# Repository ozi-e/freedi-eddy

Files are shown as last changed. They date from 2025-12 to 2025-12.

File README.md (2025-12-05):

# freedi-eddy
Adding an eddy duo probe to the qidi x-max 3 running latest freedi

I will probably add additional configurations later as I'm working on adding the LH Pico MMU also

## How to use:
### 1 - Print the bracket
I used ASA filament, it prints well without supports, I suggest adding a brim and also printing the first layer at 15mm/s
Bracket requires 2x M3 inserts

### 2 - Take off the toolhead front and back covers
Self explanatory

### 3 - Route the cable
Note: I had an idea to use an Adafruit USB C hub to chain the probe together with the toolhead, but it took a while to arrive so I used the Eddy USB cable
Route the USB cable through the e-chain, start from the toolhead and route it to the mainboard.
Roll the overlength of the cable into an "8" (don't coil it up).

### 4 - Remove the BLTouch/Inductive probe.
Screws will be re-used. You can disconnect the probe.

### 5 - Mount the Eddy probe
#### 5.1 - Remove the Eddy probe covers
#### 5.2 - Put the back cover back on, then screw it into the bracket
#### 5.3 - Mount the bracket onto the toolhead

### 6 - Back up your original config, then add or merge mine. Make sure to copy both the printer.cfg and the macros.cfg

### 7 - Add the device paths to the config
#### 7.1 - Copy the MCU toolhead path from your backup into the [mcu Toolhead] section of the new printer.cfg, then save (no restart)
#### 7.2 - In Mainsail, go to "Machine" -> "Devices" -> "Serial" -> "Refresh"
#### 7.3 - Copy the rp2040 "Path by ID" (probably on ttyACM1 if you have nothing else connected) and paste it into [mcu eddy] section of printer.cfg
#### 7.4 - Save and restart

### 8 - Copy over the begin and end codes
#### 8.1 - Paste the contents of begin_code.txt into your slicer begin code
#### 8.2 - Paste the contents of end_code.txt into your slicer end code

### 9 - Calibrate by following steps 2 through 4 (or 5 as required) from the Eddy probe onwards: https://github.com/bigtreetech/Eddy?tab=readme-ov-file#2-drive-current-calibration
Note: I already included some values regarding calibration, you should still redo everything as no 2 machines are the same
Note2: I increment the drive "reg_drive_current" to 16, your mileage may vary, check the FAQ section of the Eddy github link

### 10 - Do a test print, let me know what glitches you encounter

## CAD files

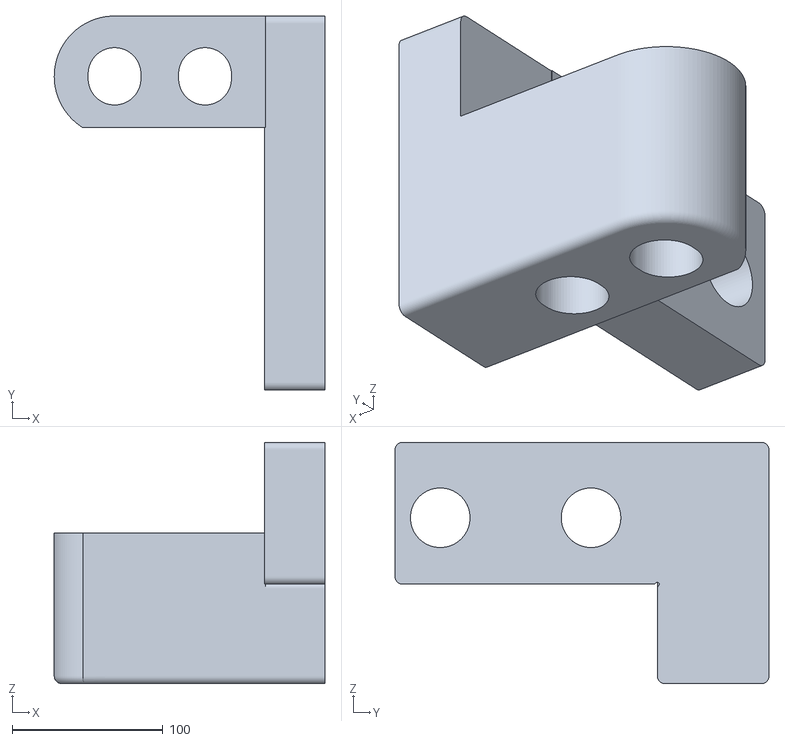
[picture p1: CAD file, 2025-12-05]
bracket.stl
179.4 x 248.0 x 160.0

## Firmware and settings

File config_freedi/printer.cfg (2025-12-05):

# X-Max3 config created by Phil1988(github)/coco.33(discord) on 20.12.2024
# For more information check out my wiki: https://github.com/Phil1988/FreeDi/wiki


#####################################################################
# Kinematics
#####################################################################
[printer]
kinematics:corexy
max_velocity: 600
max_accel: 20000
max_z_velocity: 20
max_z_accel: 500
square_corner_velocity: 8


#####################################################################
# Motherboard and periphery
#####################################################################
[temperature_sensor Mainboard_RK3328]
sensor_type: temperature_host
min_temp: 10
max_temp: 100

[mcu]
serial: /dev/ttyS0
restart_method: command
#baud: 500000

[temperature_sensor Mainboard_STM32F402]
sensor_type: temperature_mcu
sensor_mcu: mcu

[mcu Toolhead]
serial: /dev/serial/by-id/usb-Klipper_rp2040_E5D44D15290F5158-if00

[temperature_sensor Toolhead_RP2040]
sensor_type: temperature_mcu
sensor_mcu: Toolhead
min_temp: 0
max_temp: 100


#####################################################################
# Features
#####################################################################
# For saving GCODE files
[virtual_sdcard]
path: ~/printer_data/gcodes
on_error_gcode: CANCEL_PRINT

# For enabling pause/resume
[pause_resume]

# Activating exclude objects feature
[display_status]
[exclude_object]

# Expanding idle timeout
[idle_timeout]
timeout: 5400   ; 90min timeout

# Activating GCODE arc feature
[gcode_arcs]
resolution: 1.0

# Allowing free move (can be dangerous!)
[force_move]
enable_force_move: True

# Activating responses
[respond]
default_type: echo


#####################################################################
# FreeDi
#####################################################################
[include freedi.cfg] 


#####################################################################
# Macros
#####################################################################
[include macros.cfg]
#[include sp_mmu.cfg]


#####################################################################
# Input shaping
#####################################################################
[resonance_tester]
accel_chip:adxl345
probe_points:
    160, 160, 10
accel_per_hz: 75
sweeping_period: 0
max_smoothing: 0.5
    
[adxl345]
cs_pin: Toolhead:gpio13
spi_software_sclk_pin: Toolhead:gpio14
spi_software_mosi_pin: Toolhead:gpio15
spi_software_miso_pin: Toolhead:gpio12
axes_map: -x, z, -y

[input_shaper]
#shaper_type_x: mzv
#shaper_freq_x: 57.6
#shaper_type_y: mzv
#shaper_freq_y: 46.6


#####################################################################
# Hotend
#####################################################################
[extruder]
step_pin: Toolhead:gpio5
dir_pin: Toolhead:gpio4
enable_pin: !Toolhead:gpio10
rotation_distance: 53.5
gear_ratio: 1628:170
microsteps: 16
full_steps_per_rotation: 200
nozzle_diameter: 0.400
filament_diameter: 1.75
min_temp: 0
max_temp: 360
min_extrude_temp: 0
smooth_time: 0.000001
step_pulse_duration:0.000002

heater_pin: Toolhead:gpio0
sensor_type:MAX6675
sensor_pin: Toolhead:gpio17
max_power: 1.0
#control: pid  
#pid_Kp: 24.737
#pid_Ki: 10.994
#pid_Kd: 13.915

spi_speed: 100000
spi_software_sclk_pin: Toolhead:gpio18
spi_software_mosi_pin: Toolhead:gpio19
spi_software_miso_pin: Toolhead:gpio16

pressure_advance: 0.032
pressure_advance_smooth_time: 0.03
max_extrude_cross_section:5
instantaneous_corner_velocity: 10.000
max_extrude_only_distance: 1000
max_extrude_only_velocity: 130
max_extrude_only_accel: 3000

[verify_heater extruder]
max_error: 120
check_gain_time: 20
hysteresis: 5
heating_gain: 1


#####################################################################
# Heated bed
#####################################################################
[heater_bed]
heater_pin: PC8
sensor_type: NTC 100K MGB18-104F39050L32
sensor_pin: PA0
max_power: 1.0
#control: pid
#pid_kp: 64.431
#pid_ki: 2.845
#pid_kd: 364.839
min_temp: -50
max_temp: 125
pwm_cycle_time: 0.02 # for 50Hz line power 
#pwm_cycle_time: 0.016 # for 60Hz line power

[verify_heater heater_bed]
max_error: 200
check_gain_time: 360
hysteresis: 5
heating_gain: 1


#####################################################################
# Bed mesh
#####################################################################
#[bed_mesh]
#speed: 150               
#horizontal_move_z: 2.6   
#mesh_min: 28,8        
#mesh_max: 315,310     
#probe_count: 9,9     
#algorithm: bicubic
#bicubic_tension: 0.2
#mesh_pps: 4, 4


#####################################################################
# Probe
#####################################################################
#!# Pay attention to this section and compare it with your stock backup config
#[probe]
#pin: ^!Toolhead:gpio11
#x_offset: 28
#y_offset: 4.4
##z_offset: 1.890
#speed: 5
#samples: 2
#samples_result: average
#sample_retract_dist: 1.5
#samples_tolerance: 0.08
#samples_tolerance_retries: 3


#####################################################################
# Heated chamber
#####################################################################
[heater_generic chamber]
heater_pin: PB10
max_power:1.0
sensor_type:NTC 100K MGB18-104F39050L32
sensor_pin: PA1
control: watermark
max_delta: 1.0
min_temp:-100
max_temp:70

[verify_heater chamber]
max_error: 300
check_gain_time:480
hysteresis: 5
heating_gain: 1


########################################
# Filament runout sensor
########################################
[filament_switch_sensor filament]
switch_pin: ^Toolhead:gpio21
pause_on_runout: True
runout_gcode:
            M118 Filament run out!
event_delay: 3.0
pause_delay: 0.5


#####################################################################
# Fans
#####################################################################
## Part cooling fan 
# [fan_generic partfan]
# pin: Toolhead:gpio2
# max_power: 1.0
# cycle_time: 0.0100
# hardware_pwm: false
# kick_start_time: 0.200
# off_below: 0.08
# shutdown_speed: 0
[fan]
pin: Toolhead:gpio2
max_power: 1.0
cycle_time: 0.0100
hardware_pwm: false
kick_start_time: 0.200
off_below: 0.08
shutdown_speed: 0.0

## Big side radial turbo fan
[fan_generic sidefan]
pin: PA8
max_power: 1.0
cycle_time: 0.0100
hardware_pwm: false
kick_start_time: 0.250
off_below: 0.3
shutdown_speed: 0

## Activated charcoal blowing fan
[fan_generic filterfan]
pin: PC9
max_power: 1.0
cycle_time: 0.0100
hardware_pwm: false
kick_start_time: 0.200
off_below: 0.3
shutdown_speed: 0

## Cold end and toolhead housing fans
[heater_fan hotend_fan]
pin: Toolhead:gpio1
max_power: 1.0
shutdown_speed:1.0
kick_start_time: 0.5
heater: extruder
heater_temp: 50.0
fan_speed: 1.0
off_below: 0

#!# Delete the next section if your stock backup config doesnt have it
# Toolhead cooling fan
[heater_fan hotend_fan2]
pin: Toolhead:gpio20
max_power: 1.0
kick_start_time: 0.5
heater: extruder
heater_temp: 50.0
fan_speed: 1.0
off_below: 0

#!# Delete the next section if your stock backup config doesnt have it
## Controllable Mainboard cooling fan
[temperature_fan Mainboard_fan]
sensor_type: temperature_host 
pin: PC4        
max_power: 1.0  
cycle_time: 0.01
sensor_type: temperature_combined
sensor_list: temperature_sensor Mainboard_RK3328, temperature_sensor Mainboard_STM32F402
combination_method: max                                           # use the maximum reading of the sensors
maximum_deviation: 999.9                                          # we don't care about the difference in temperature
shutdown_speed: 0.0
kick_start_time: 0.4
off_below: 0.19
min_temp: 0
max_temp: 85.0  
target_temp: 42.0
min_speed: 0
max_speed: 1.0
control: pid
pid_deriv_time: 2.0
pid_Kp: 2.0
pid_Ki: 5.0
pid_Kd: 0.5


#####################################################################
# Light
#####################################################################
## caselight LEDs
[output_pin caselight]
pin: PC7
pwm: true
cycle_time: 0.0100
shutdown_value:0
value:1


#####################################################################
# Buzzer
#####################################################################
## Buzzer
[output_pin buzzer]
pin: PA2
pwm: false
shutdown_value:0
value:0

[output_pin sound]
pin: PA13
value:0


#####################################################################
# Power outage shutdown
#####################################################################
[output_pin pwc]
pin: PA3
pwm: False
value: 1
shutdown_value: 1


#####################################################################
# Drives
#####################################################################
[stepper_x]
step_pin: PB4
dir_pin: PB3
enable_pin: !PB5
microsteps: 32
rotation_distance: 39.94
full_steps_per_rotation: 200 
endstop_pin: tmc2209_stepper_x:virtual_endstop
position_min: -4
position_endstop: 334
position_max: 334
homing_speed: 40
homing_retract_dist: 0
homing_positive_dir: True
step_pulse_duration: 0.000002
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

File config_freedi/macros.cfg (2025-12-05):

#####################################################################
# Advanced CHAMBER_TEMP_CONTROLLER
#####################################################################

[gcode_macro SET_PRINT_STATS_INFO]
rename_existing: BASE_SET_PRINT_STATS_INFO_BASE
gcode:
    #TIMELAPSE_TAKE_FRAME
    BASE_SET_PRINT_STATS_INFO_BASE {rawparams}
    CHAMBER_TEMP_CONTROLLER

# Safety macro that gets frequently called by SET_PRINT_STATS_INFO to prevent too high chamber temperatures
[gcode_macro CHAMBER_TEMP_CONTROLLER]
gcode:
    {% set chamber_target_temp = printer['heater_generic chamber'].target %}
    {% set chamber_temp = printer['heater_generic chamber'].temperature %}
    {% if chamber_temp > printer.configfile.settings['heater_generic chamber'].max_temp %}
        M106 P3 S255
    {% else %}
        {% if chamber_target_temp > 0 %}
            # Allow for 3C of "grace" before we start ramping the exhaust fan speed
            # This prevents the macro from fighting with the chamber heater PID algorithm
            {% set difference = chamber_temp - (chamber_target_temp + 3) %}
            {% if difference > 0 %}
                {% set filterfan_speed = ([(difference * 50), 255] | min) | int %}
                M106 P3 S{filterfan_speed}
            {% else %}
                M106 P3 S0
            {% endif %}
        {% endif %}
    {% endif %}
    
    
#####################################################################
# Homing modification
#####################################################################
[gcode_macro G28]
rename_existing: G28.1
gcode:
    {% set reduced_current_x = 0.6 %}
    {% set reduced_current_y = 0.7 %}
    {% set home_all = ('X' in rawparams.upper() and 'Y' in rawparams.upper() and 'Z' in rawparams.upper()) or 
                      ('X' not in rawparams.upper() and 'Y' not in rawparams.upper() and 'Z' not in rawparams.upper()) %}
    {% set home_current_x = printer.configfile.settings['tmc2209 stepper_x'].run_current * reduced_current_x %}
    {% set home_current_y = printer.configfile.settings['tmc2209 stepper_y'].run_current * reduced_current_y %}

    {% set init_XY_move = 30 %}
    #{% set y_init_move = 5 %}
    {% set z_clearance = 2 %}

    {% set home_all_final_position_x = printer.toolhead.axis_maximum.x / 2 %}
    {% set home_all_final_position_y = printer.toolhead.axis_maximum.y - 40 %}
    {% set home_all_final_position_z = 20 %}

    # If homing should at least move X or Y axis
    {% if home_all or 'X' in rawparams.upper() or 'Y' in rawparams.upper() %}     
        # Check if Z is homed
        {% if 'z' in printer.toolhead.homed_axes %}
            {% set Z_axis_was_homed = true %}                                                                       ; Set Z_axis_was_homed to true if Z is already homed
            G91                                                                                                     ; Use relative positioning
            G1 Z2 F600                                                                                              ; Move bed down
            G90                                                                                                     ; Use absolute positioning
        {% else %}
            {% set Z_axis_was_homed = false %}                                                                      ; Set Z_axis_was_homed to false if Z is not homed
            FORCE_MOVE STEPPER=stepper_z DISTANCE={z_clearance} VELOCITY=10                                         ; Move bed down
        {% endif %}
    {% endif %}

    {% if home_all or 'X' in rawparams.upper() or 'Y' in rawparams.upper() %} 
        G91                                                                                                         ; Use relative positioning
        FORCE_MOVE STEPPER=stepper_x DISTANCE={init_XY_move} VELOCITY=40                                            ; Move X a little before homing
        SET_KINEMATIC_POSITION X={printer.toolhead.position.x + (init_XY_move/2)}                                   ; Compensate the FORCE_MOVE position 
        SET_KINEMATIC_POSITION Y={printer.toolhead.position.y + (init_XY_move/2)}                                   ; Compensate the FORCE_MOVE position 
        G90                                                                                                         ; Use absolute positioning
    {% endif %}

    # Home X
    {% if home_all or 'X' in rawparams.upper() %}        
        SET_TMC_CURRENT STEPPER=stepper_x CURRENT={home_current_x}                                                  ; Lower motor current
        SET_TMC_CURRENT STEPPER=stepper_y CURRENT={home_current_x}                                                  ; Lower motor current
        G28.1 X                                                                                                     ; Home X
        SET_TMC_CURRENT STEPPER=stepper_x CURRENT={printer.configfile.settings['tmc2209 stepper_x'].run_current}    ; Set motor current to the previous value
        SET_TMC_CURRENT STEPPER=stepper_y CURRENT={printer.configfile.settings['tmc2209 stepper_y'].run_current}    ; Set motor current to the previous value
        #G1 X290 F1200                                                                                                ; Move X-axis slightly
        #G91
        #G1 X-10 F1200
        #FORCE_MOVE STEPPER=stepper_y DISTANCE=-10 VELOCITY=40
        #G90
    {% endif %}
    
    # Home Y
    {% if home_all or 'Y' in rawparams.upper() %}
        SET_TMC_CURRENT STEPPER=stepper_x CURRENT={home_current_y}                                                  ; Lower motor current
        SET_TMC_CURRENT STEPPER=stepper_y CURRENT={home_current_y}                                                  ; Lower motor current
        G28.1 Y                                                                                                     ; Home Y
        SET_TMC_CURRENT STEPPER=stepper_x CURRENT={printer.configfile.settings['tmc2209 stepper_x'].run_current}    ; Set motor current to the previous value
        SET_TMC_CURRENT STEPPER=stepper_y CURRENT={printer.configfile.settings['tmc2209 stepper_y'].run_current}    ; Set motor current to the previous value
        #G1 Y10 F1200                                                                                                ; Move Y-axis slightly
        #G91
        #G1 Y10 F1200
        #FORCE_MOVE STEPPER=stepper_y DISTANCE=-10 VELOCITY=40
        #G90
    {% endif %} 

    # Raise the bed again if only X or only Y axes were homed
    {% if not (home_all or 'Z' in rawparams.upper()) %}
        {% if Z_axis_was_homed %}
            G91                                                                                                     ; Use relative positioning
            G1 Z-2 F600                                                                                             ; Raise the bed back again
            G90                                                                                                     ; Use absolute positioning
        {% else %}
            FORCE_MOVE STEPPER=stepper_z DISTANCE=-{z_clearance} VELOCITY=10                                        ; Raise the bed back again
        {% endif %}
    {% endif %}

    # Home Z
    {% if home_all or 'Z' in rawparams.upper() %}
        G28.1 Z                                                                                                     ; Home Z
        G90                                                                                                         ; Set absolute positioning
        G1 Z{home_all_final_position_z}                                                                             ; Move bed down
    {% endif %}

    # Move to the final position if all axes were homed
    {% if home_all %}
        G90                                                                                                         ; Set absolute positioning
        G1 X{home_all_final_position_x} Y{home_all_final_position_y} Z{home_all_final_position_z} F7800             ; Move to the rear center
    {% endif %}


# Unconditional stop
[gcode_macro M0]
gcode:
    PAUSE


# Pause SD print
[gcode_macro M25]
rename_existing: M9925
gcode:
    PAUSE
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

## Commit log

2025-12-05 Initial commit - working freedi config
    added x-max 3 config, front-right homing, eddy duo coil support with adaptive mesh
    "works for me"
    [freedi.cfg, macros.cfg, printer.cfg]
2025-12-05 Update README with installation instructions for Eddy probe
    Expanded instructions for installing and configuring the Eddy probe on the Qidi X-Max 3, including detailed steps and notes.
2025-12-05 Update README with installation steps for Eddy probe
2025-12-05 Added bracket stl file
    [bracket.stl]
2025-12-05 Update README with M3 insert requirement
    Added note about required M3 inserts for bracket.
